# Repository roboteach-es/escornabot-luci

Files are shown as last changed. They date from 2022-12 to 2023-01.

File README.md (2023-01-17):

# Escornabot Luci

En base á nosa propia experiencia docente co [**Escornabot Brivoi**](https://www.escornabot.org/wiki/index.php?title=Archivo:Brivoi-001.jpg), xurdiu a necesidade de crear unha nova *subespecie* (ou versión). Baseada no Brivoi, incorporámoslle un sistema de **alimentación recargable** que axuda en varias frontes:

1. Supresión das pilas (aforro económico e ecolóxico)
2. Maior tempo de uso (maior cantidade de enerxía)
3. Facilidade de uso (basta con recargar, sen montar/desmontar para cambiar pilas)
4. Ideal para facer reciclaxe (cargadores de móbil, baterías de portátiles etc.)

Somos conscientes tamén das contraindicacións do emprego de baterías, e tivéronse en conta á hora de deseñar esta subespecie (por exemplo, **a seguridade**). Tamén coidamos todo o posible **o equilibrio** entre a dificultade de fabricación, o coste dos materiais e a usabilidade/practicalidade, xa que un dos obxectivos fundamentais é **a ACCESIBILIDADE** (en sentido amplo!).

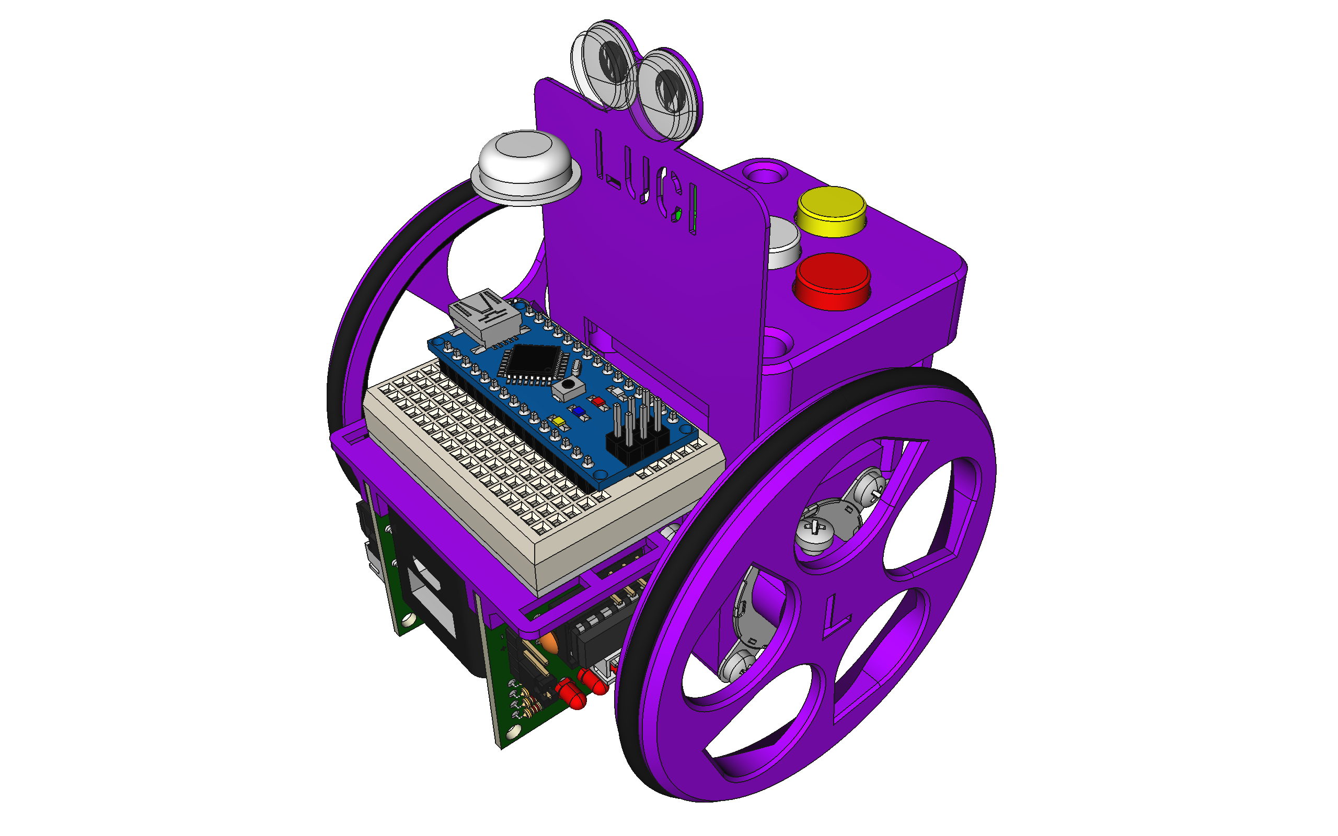
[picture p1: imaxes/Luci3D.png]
Luci 3D

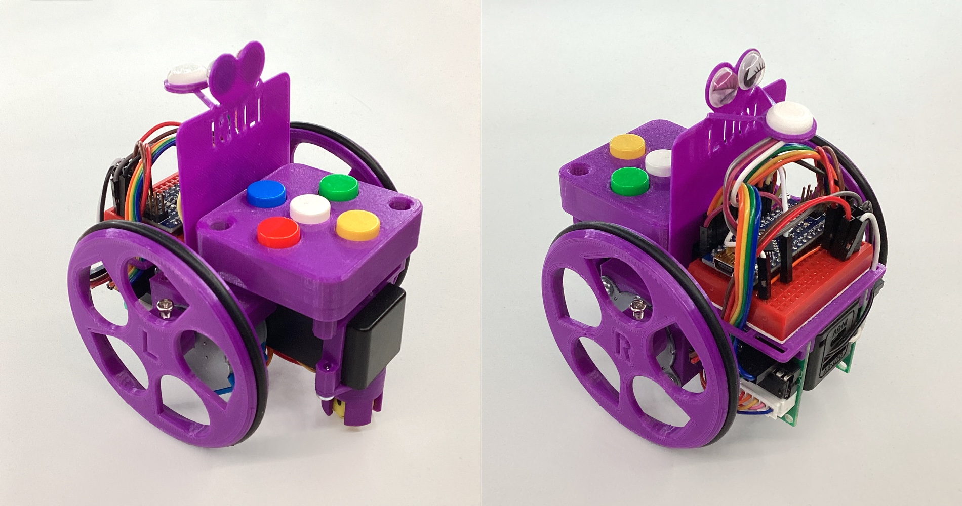
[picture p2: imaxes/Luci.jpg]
Luci prototipo


Continuando coa tradición do sistema de nomeclatura do proxecto Escornabot, decidimos bautizalo empregando unha das subespecies, escollendo a [subespecie **Luci**](https://species.wikimedia.org/wiki/Lucanus_luci) por tratarse dun nome **feminino** e relativo á **luz**. E a cor identificativa: **violeta** (claramente! 🙆🏽‍♀️😊)

## NOVIDADES

**Luci** trae unhas cantas novidades:

* **Batería recargable**, gracias a un *PowerBank-DIY*
* **LED RGB**, gracias a un *NeoPixel*
* **Chasis 3D**, adaptado ao novo sistema de alimentación
* **Firmware**, para dar soporte ás novas funcións
* **Biblioteca programable**, na que se basea o *Firmware*

Físicamente, **Luci** é moi similar ao **Brivoi** do que parte, con apenas 5 mm de ancho adicionais, conservando o **factor de forma** que todas coñecemos (e tanto nos gusta), polo que podes usalo exactamente **igual que o anterior**. Leva a mesma cantidade de tornillos e segue sendo igual de fácil de montar. O **coste de fabricación** tamén é moi similar, incluso mais económico se consegues facer **reciclaxe de baterías**. A maior vantaxe económica (e ecolóxica) é, sen embargo, o **aforro a longo prazo**, xa que podes recargalo e non terás que mercar (nin tirar) mais pilas.

**Luci** está en continuo desenvolvemento, e ainda é un *traballo en marcha*: se descubres calqueira problema, ou queres facer algunha aportación, por favor **contacta con nos**, estaremos encantadas de saber de ti.

## QUERO UN, como fago?

Se queres un **Escornabot Luci** podes acudir á [**guía de fabricación**](FABRICACIÓN.md) para facerte tantos como queiras: nela explicamos todo o necesario, dende a merca de compoñentes, pasando pola impresión 3D ate a reciclaxe de baterías.

## INFORMACIÓN

O proxecto **Luci** está conformado por diversos apartados que se recollen a continuación:

### HARDWARE

Na carpeta [`3D`](3D) atoparás todos os **modelos 3D** editables das pezas, creadas usando [FreeCAD](https://freecad.org). Tamén están dispoñibles os **ficheiros STL**, listos para ser impresos en 3D.

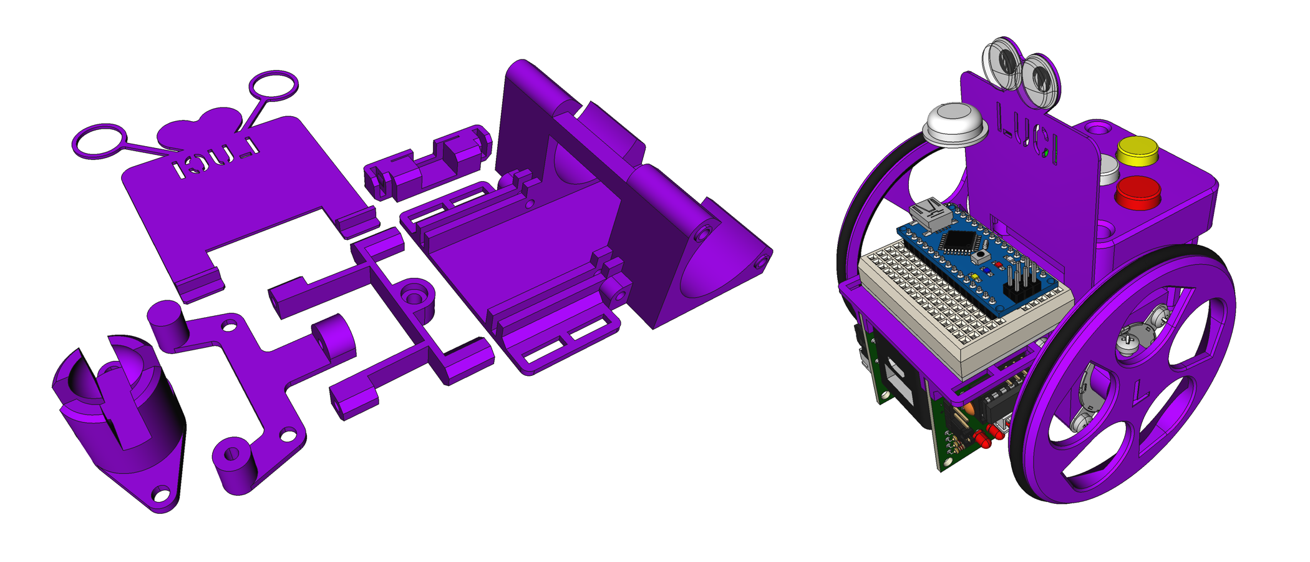
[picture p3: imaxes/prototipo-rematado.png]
Pezas3D


O compoñente central de Luci é o [PowerBank-DIY](POWERBANK.md), que está documentado no seu propio apartado.

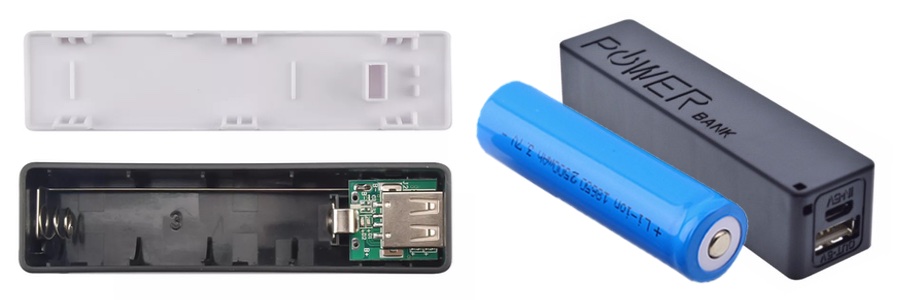
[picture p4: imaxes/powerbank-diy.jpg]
PowerBank-DIY


Na carpeta [`Electrónica`](Electrónica) atoparás o esquema de conexionado, creado con [Fritzing](https://fritzing.org).

Connections

### SOFTWARE

Na carpeta [`Programación`](Programación) atoparás todo o relativo ao apartado de programación, ainda que a [**biblioteca programable e o Firmware**](https://github.com/roboteach-es/escornabot-lib) teñen o seu propio repositorio específico.

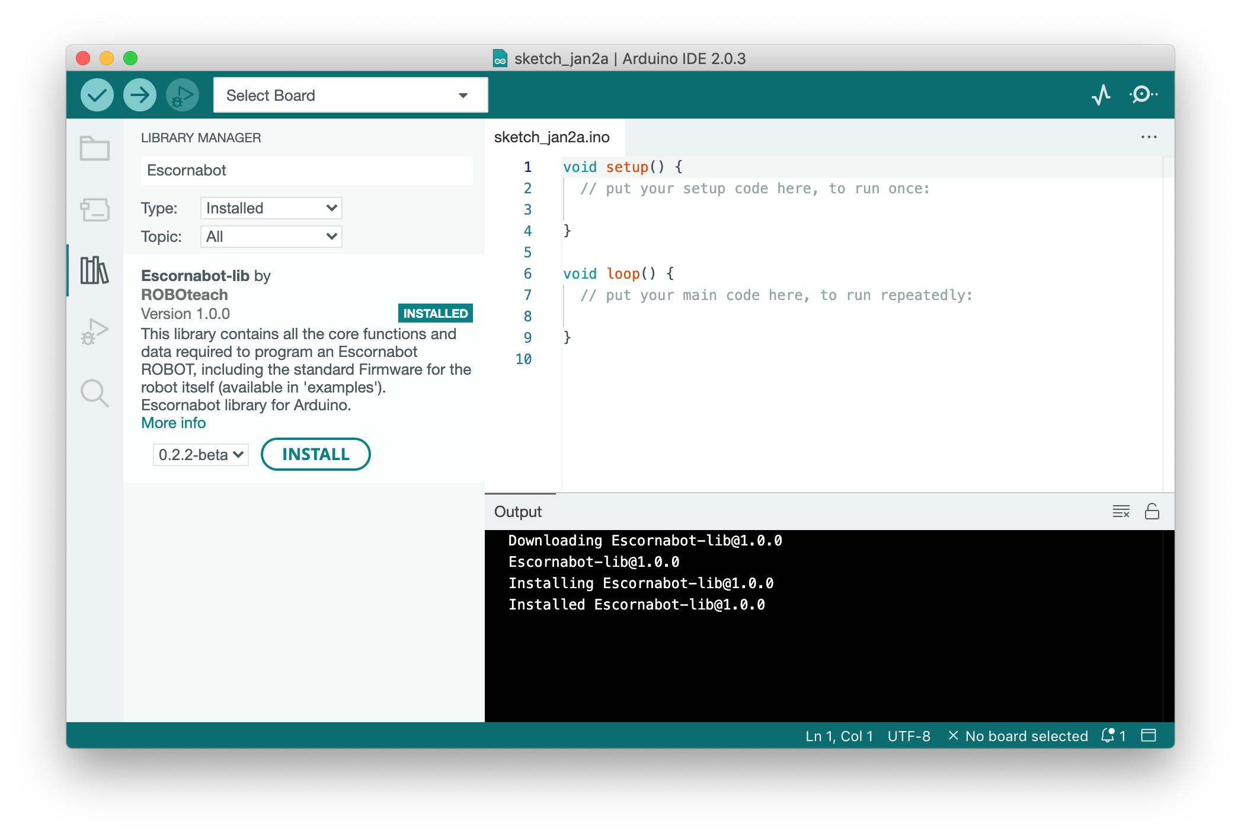
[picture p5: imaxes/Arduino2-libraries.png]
Biblioteca Arduino (https://github.com/roboteach-es/escornabot-lib)


### BITÁCORA

Se queres saber detalles do desenvolvento, levamos unha especie de bitácora que [podes ler](DESENVOLVEMENTO.md).

## LICENZA

Este traballo está suxeito á licenza [GNU General Public v3.0 License](LICENSE-GPLV30). Todos os ficheiros multimedia e de datos que non sexan código fonte están suxeitos á licenza [Creative Commons Attribution 4.0 BY-SA license](LICENSE-CCBYSA40).

Máis información acerca destas licenzas en [licenzas Opensource](https://opensource.org/licenses/) e [licenzas Creative Commons](https://creativecommons.org/licenses/).

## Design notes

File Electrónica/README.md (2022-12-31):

# Escornabot Luci - Electrónica

Este é o esquema de conexións de **Luci**:

Conexionado Luci

Está feito con [Fritzing](https://fritzing.org) e tes o ficheiro editable [dispoñible para descarga](Luci_conexi%C3%B3ns.fzz).

Este é o resumo de conexións entre os pins de cada **dispositivo** (á esquerda) e os pins do **Arduino Nano** (á dereita):

* **Motor Esquerdo**:
	* `IN1 ⟶ D4`
	* `IN2 ⟶ D5`
	* `IN3 ⟶ D6`
	* `IN4 ⟶ D7`
	* `GND ⟶ GND`
	* `VCC ⟶ 5V`
* **Motor Dereito**:
	* `IN1 ⟶ D8`
	* `IN2 ⟶ D9`
	* `IN3 ⟶ D10`
	* `IN4 ⟶ D11`
	* `GND ⟶ GND`
	* `VCC ⟶ 5V`
* **Teclado**:
	* `SIG ⟶ A0`
	* `GND ⟶ GND`
* **Buzzer**:
	* `PIN1 ⟶ GND`
	* `PIN2 ⟶ D2`
* **Neopixel**:
	* `IN  ⟶ D12`
	* `GND ⟶ GND`
	* `VCC ⟶ 5V`
* **PowerBANK-DIY**:
	* `5V  ⟶ 5V`
	* `GND ⟶ GND`

Para poder ter suficientes puntos de conexión para 5V e GND, hai un par de cables (os que están horizontais) que levan estes pins a cada unha das columnas laterais da *mini-breadboard*.

## Arduino Nano

**Luci** emprega un microncontrolador Arduino Nano como *cerebro* para o seu funcionamento. Aquí tes unha referencia dos pins do mesmo:

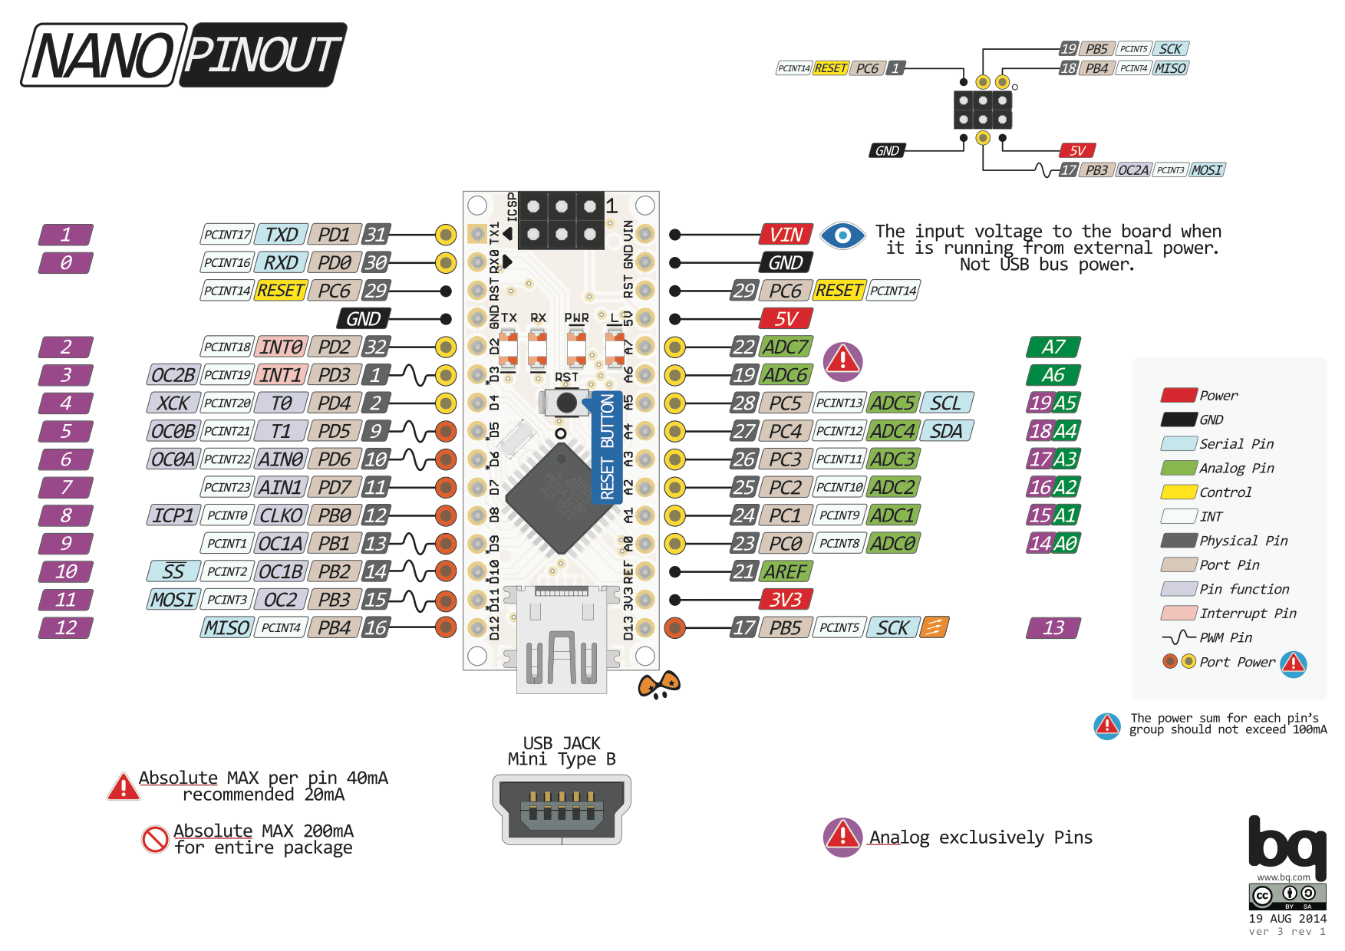
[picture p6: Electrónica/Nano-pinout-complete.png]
Arduino Nano pins


## LICENZA

Este traballo está suxeito á licenza [GNU General Public v3.0 License](../LICENSE-GPLV30). Todos os ficheiros multimedia e de datos que non sexan código fonte están suxeitos á licenza [Creative Commons Attribution 4.0 BY-SA license](../LICENSE-CCBYSA40).

Máis información acerca destas licenzas en [licenzas Opensource](https://opensource.org/licenses/) e [licenzas Creative Commons](https://creativecommons.org/licenses/).

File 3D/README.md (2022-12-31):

# Escornabot Luci - 3D

Este é o modelo 3D de **Luci**:

Luci

Estas son as pezas novas para esta subespecie:

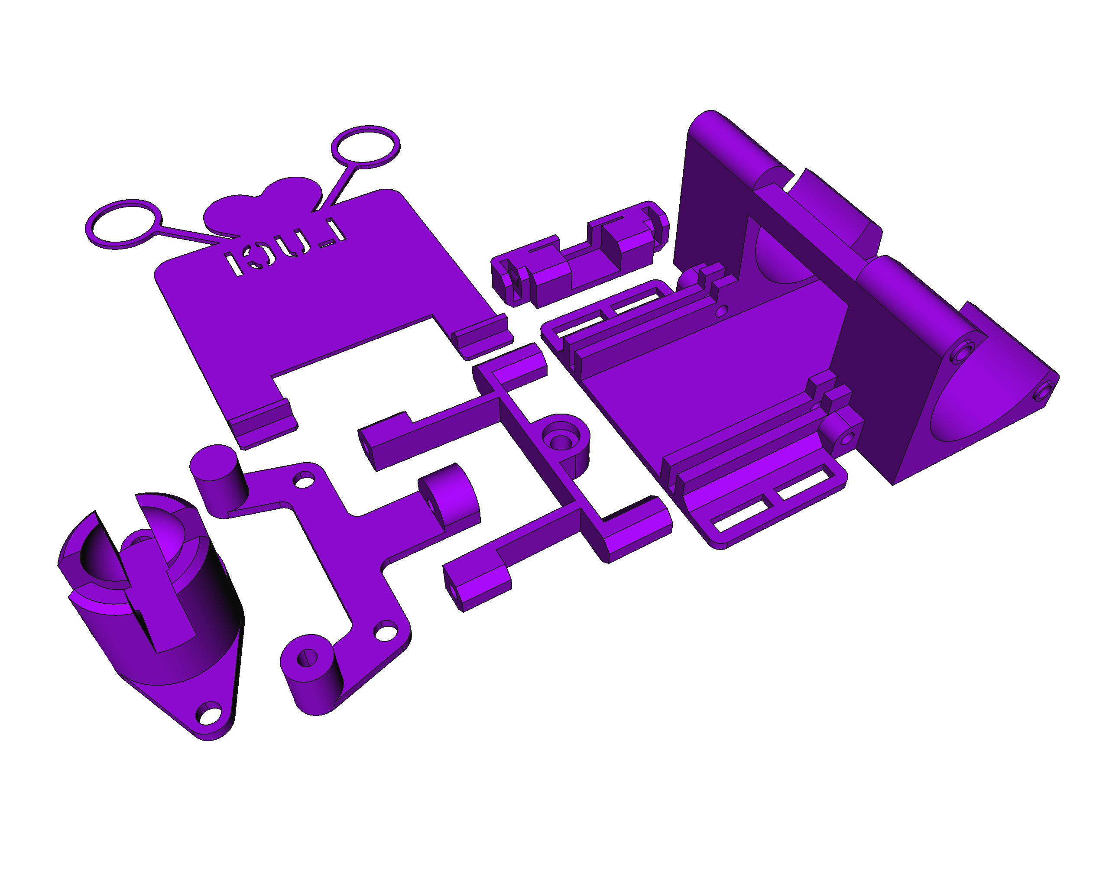
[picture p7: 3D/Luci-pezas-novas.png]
Novas pezas


de esquerda a dereita: **porta-bola**, **carauta NeoPixel**, **soporte teclado**, **soporte porta-bola**, **soporte interruptor** e **chasis**.

## Modelos 3D editables

Todos os modelos 3D foron creados coa ferramenta open-source [FreeCAD](https://www.frecad.org), e están dispoñibles para a súa edición:

* [`Escornabot-Luci.FCStd`](Escornabot-Luci.FCStd), modelo principal (o da imaxe) que contén tódalas novas pezas
* [`keypad-cover.FCStd`](keypad-cover.FCStd), a coberta do teclado
* [`wheel-left.FCStd`](wheel-left.FCStd) e [`wheel-right.FCStd`](wheel-right.FCStd), as rodas
* [`wheel-base.FCStd`](wheel-base.FCStd), a roda base, por se queres personalizala
* [`Escornaface-NeoPixel.FCStd`](Escornaface-NeoPixel.FCStd), carauta separada, por se queres personalizala

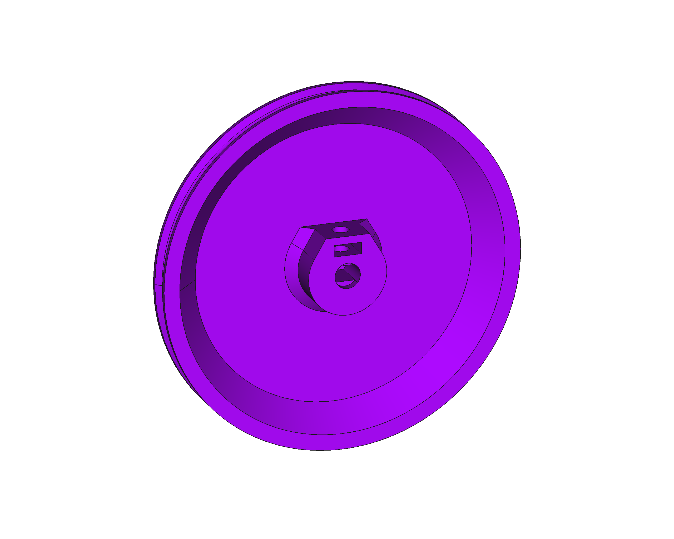
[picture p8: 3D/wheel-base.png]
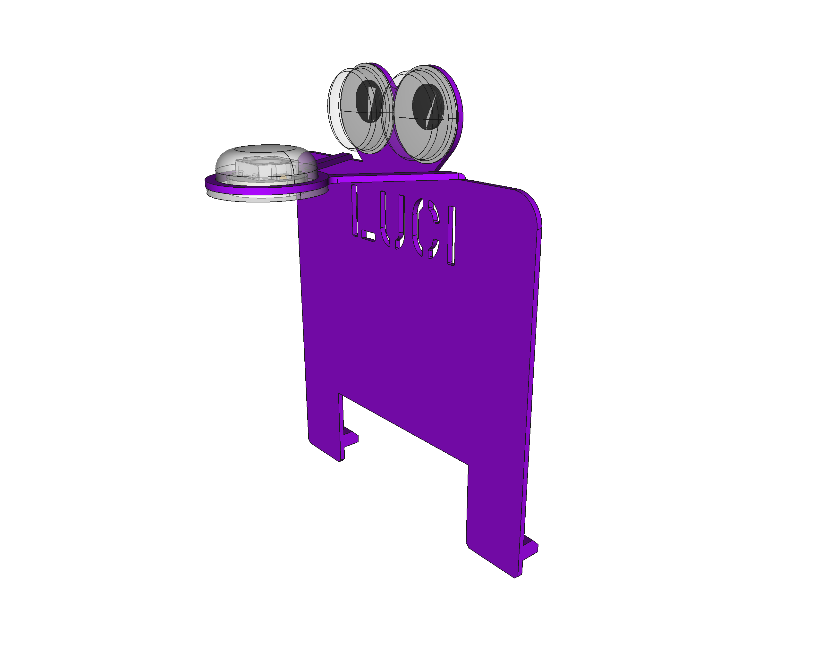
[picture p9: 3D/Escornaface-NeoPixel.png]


## Listado STL

Na carpeta [`stl`](stl) poderás atopar todos os ficheiros das 10 pezas, listas para ser impresas con calqueira impresora 3D.

Pezas novas:

* [`Porta-bola`](stl/luci-ballcaster.stl)
* [`Carauta NeoPixel`](stl/luci-escornaface-NP.stl)
* [`Soporte teclado`](stl/luci-keypad-chasis-support.stl)
* [`Soporte porta-bola`](stl/luci-keypad-ballcaster-support.stl)
* [`Soporte interruptor`](stl/luci-switch-holder.stl)
* [`Chasis`](stl/luci-chasis.stl)
* [`Cápsula NeoPixel`](stl/luci-neopixel.stl) (non aparece na imaxe anterior)

Pezas reutilizadas:

* [`Roda esquerda`](stl/wheel-left.stl)
* [`Roda dereita`](stl/wheel-right.stl)
* [`Cubre teclado`](stl/keypad-cover.stl)

## LICENZA

Este traballo está suxeito á licenza [GNU General Public v3.0 License](../LICENSE-GPLV30). Todos os ficheiros multimedia e de datos que non sexan código fonte están suxeitos á licenza [Creative Commons Attribution 4.0 BY-SA license](../LICENSE-CCBYSA40).

Máis información acerca destas licenzas en [licenzas Opensource](https://opensource.org/licenses/) e [licenzas Creative Commons](https://creativecommons.org/licenses/).

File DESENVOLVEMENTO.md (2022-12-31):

# DESENVOLVENTO de Luci

Algunhas notas sobre o proceso de desenvolvemento de Luci. Non é algo riguroso ou
sistemático, soamente unha especie de *bitácora*.

## Arrinque
O desenvolvemento de **Luci** comezou a finais do 2021: fartas do problema das
pilas decidimos intentar -en serio(™)- facer unha versión baseada nun
[*powerbank-DIY*](POWERBANK.md), reutilizando celas 18650 Li-ion recicladas de
baterías de portátiles vellos ou estropeados.

powerbank-diy

O obxectivo era facelo **accesible**, simple e o mais seguro posible:

* Compoñentes económicos e fáciles de atopar
* Montaxe simple, apto para calqueira nivel
* Seguro, empregando kits prefabricados con mecanismos de protección
* Principio das múltiples R (Reducir, Reutilizar, Reciclar, Recuperar, Reparar ...)
* Principio de deseño [KISS](https://en.wikipedia.org/wiki/KISS_principle)

Empezamos collendo os compoñentes físicos e posicionandoos, probando distintas
configuracións para tratar de ver que funcionaba e que sensacións tiñamos, discutindo
sobre que podería funcionar ou que problemas poderiamos ter.

## 1 xaneiro 2022
A última acción do 2021 e primeira do 2022 foi publicar o repositorio git do
proxecto en [github](https://github.com/roboteach-es/escornabot-luci): tratábase
dunha proba de concepto onde, nun modelo 3D en [FreeCAD](https://freecad.org),
posicionamos todos os compoñentes de Luci (motores+drivers, mini-breadboard+arduino,
teclado, rodas, bola-tola e powerbank) tal e como decidiramos na discusión previa.

Foi o nacemento **oficial e formal** público do proxecto.

## 8-9 decembro 2022
**Despois de case un ano** sen ningunha actividade, retomouse o deseño 3D en FreeCAD
para tratar de crear un chasis funcional. Partindo do traballo previo, fixéronse
ata tres versións distintas con múltiples iteracións para axustar pequenas cousas,
ata chegar ao primeiro esqueleto que permitía montar todos os compoñentes.

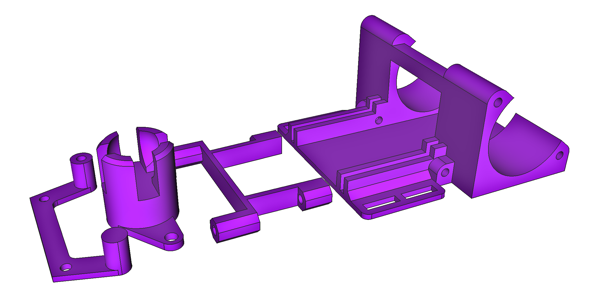
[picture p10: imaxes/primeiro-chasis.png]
primeiro chasis


O mais salientable é que a peza do chasis, a pesar desa ponte de 25mm, pódese imprimir 
perfectamente sen soportes (nunha impresora básica calqueira como pode ser a *Ender-3*).

## 10 decembro 2022
Probando o primeiro prototipo apareceron algúns problemas, as veces menores e
outros non tanto:

* **Equilibrio**: Luci balacéase con facilidade, xa que a cela 18650 non pesa
  tanto como as pilas e o centro de gravidade esta moi próximo aos eixos de
  rotación no punto central. Cun pequeno refinamento mellorou, pero seguirá
  sendo a mais equilibrista (o que pode acabar convertíndose no seu selo de
  identidade 😅💃🏽)
* **Cables**: *arboran* con facilidade e os conectores dupont deron moita guerra
   co espacio que ocupan. Cunhas pequenas guías para os cables e algúns axustes de
  posición, acabaron encaixando.
* **Autoapagado**: a maioría dos *powerbank* teñen unha función de autoapagado
  e se desconectan se non detectan suficiente consumo de enerxía. O consumo de
  Luci en reposo non é suficiente para evitalo, e este problema... non é trivial.

### Autoapagado
Cando Luci está en movemento, o consumo (dos motores) é suficiente alto e non hai
problema, pero o tempo de reposo máximo é pequeno (uns poucos segundos) e, ademáis,
o comportamento varía dun powerbank a outro:

* **HT4928S**: estando Luci en reposo e, aproximadamente aos 12 seg., salta o
  autoapagado. Unha vez apagado, actívase o modo de detección de "nova conexión" e,
  como hai algo conectado, volve a acenderse. É dicir, temos un círculo vicioso de
  reinicios cada 12 seg.: non consume o suficiente para manterse acendido pero
  si consume o suficiente para reacenderse. 🤷🏽‍♂️
* **TP4333**: o consumo mínimo é maior, pero cando se apaga, realmente queda
  apagado (non se reinicia).

Ambos comportamentos teñen os seus PROs e CONTRAs, e barállanse varias opcións
para "resolvelo":

* engadir unha carga paralela permanente (LEDs)? (maior consumo, mais complexidade...)
* incluir no *firmware* un sistema *anti-reposo* como, por exemplo, acender bobinas
  periódicamente en caso de inactividade (probablemente a opción menos mala...)
* en último caso... facer un powerbank dende cero? (non cumpre o principio KISS)

En calqueira caso, un firmware novo é unha tarefa longamente requerida (e
postergada)...

## 11-12 decembro 2022
Prototipo inicial rematado, con algunhas modificacións extra e un par de novas
pezas: soporte do interruptor e a carauta.

powerbank-diy

Agora hai que deixalo *"respirar"* e probar a usalo **no campo** para descubrir
que cousas hai que corrixir ou mellorar. Algún *early-adopter* léndonos?

**PROBLEMAS:** o conector USB queda escondido trala roda (hai que quitala para poder
conectar o cable).<br />
**PORFACER:** programar un novo firmware con anti-reposo.

## 16-25 decembro 2022
**Luci** non ía ser moi útil sen software, e os problemas, complexidade e
sobre-enxeñería do [firmware *oficial*](https://github.com/escornabot/arduino),
non convidaban a seguir *meténdolle mais horas(™)*, así que creamos unha
[*suite* **completamente nova**](https://github.com/roboteach-es/escornabot-lib),
partindo dende cero e aproveitando a experiencia recollida, primeiro do firmware
anterior (que ten moitas cousas boas) e, sobre todo, da nosa propia labor
\[docente\] de campo, tras empregar o Escornabot en moitos e moi variados
escenarios formativos e didácticos.

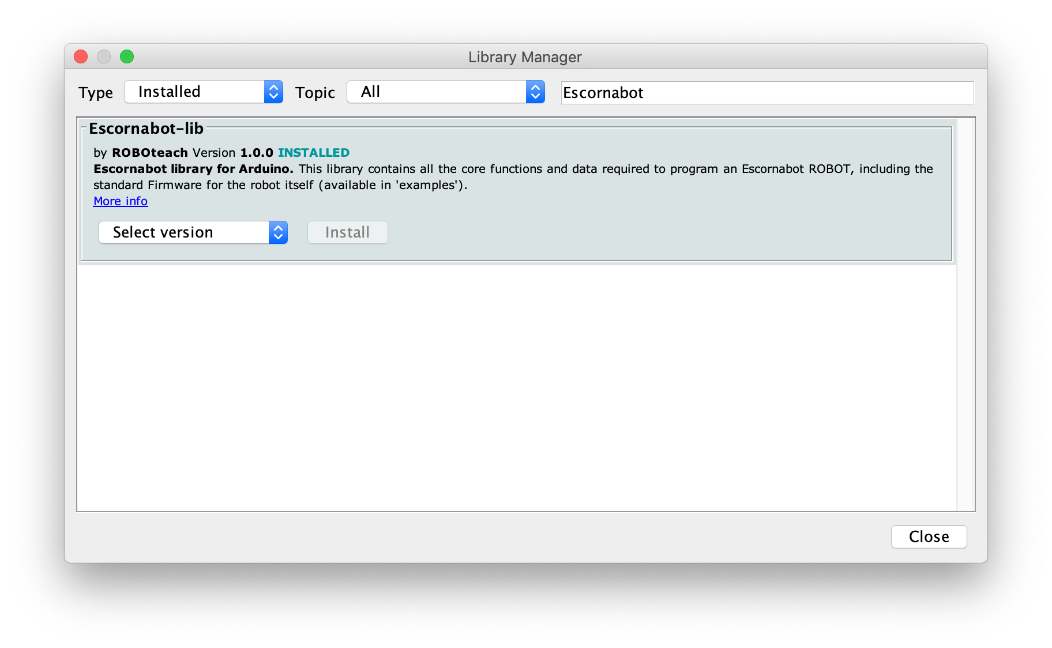
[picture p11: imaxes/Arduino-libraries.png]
Escornabot-lib


Esta nova *suite* está publicada a través da propia **plataforma de Arduino**,
de maneira que aparece como unha bibliteca instalable directa e automaticamente
a través do [seu IDE](https://www.arduino.cc/en/software). Componse de:

* unha **biblioteca base** que recolle todas as funcionalidades fundamentais
* un conxunto de **exemplos** onde se ilustra o seu emprego
* un novo **firmware** que está escrito a partires dela

Deste xeito, ademáis de simplificarse moito, abstráese o núcleo, o que resulta
moi convinte para outras áreas como a integración con ferramentas de terceiros
(por exemplo, a contorna de programación visual *mBlock-3* &rarr; `TODO`).

O novo sistema está deseñado **específicamente para Luci** e, para poder
alcanzar o que nos propusimos inicialmente, hai certos aspectos que son únicos
e \[inicialmente\] incompatibles co anteriormente existente:

* novo [**esquema de conexionado**](Electrónica) optimizado para Luci (alimentación 5V)
* sistema de control de motores optimizado ([empregando
  *PORTx*](https://github.com/mgesteiro/steppers#portx-vs-digitalwrite))
* resolución do [**problema do autoapagado**](#autoapagado) dos *powerBank*
* control de inactividade
* autoconfiguración do teclado
* incorporación dun NeoPixel (LED RGB)
* resolución de problemas de interfaz e UX (botón azul)
* e soporte correcto para RTTTL

Esta suite está xa dispoñible no seu propio 
[repositorio **Escornabot-lib**](https://github.com/roboteach-es/escornabot-lib).

## 30-31 decembro 2022
Último millón de axustes e READMEs y mil pequenas cousas mais para a publicación
final de **Luci**: xusto **un ano despois**.

Queda moito por facer, pero é unha boa base de partida, con moitos **hitos
importantes** alcanzados:

* Prototipo hardware rematado e validado (pódese fabricar!)
* Suite de software completa, con todas as funcionalidades orixinais (pódese programar!)
* Documentación base rematada (está documentado!)

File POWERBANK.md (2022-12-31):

# PowerBank-DIY

Unha pequena *intro* aos **PowerBank-DIY** (_**D**o **I**t **Y**ourself_ = Faino Ti Mesma): son kits para fabricarte as túas propias *baterías-recargables* empregando -tipicamente- celas estándar 18650 Li-ion. O kit trae unha caixa contenedora (normalmente de ABS) cunha tapa autopechante. Ten espazo para unha cela 18650 (**NON INCLUÍDA**) e leva incorporada unha pequena circuitería electrónica (con **dous portos USB** distintos) que se encarga de toda a xestión.

powerbank-diy

A **carga** do PowerBank-DIY efectúase a través do porto **micro-USB**, empregando -por exemplo- un cargador de móbil (dos antigos). A nerxía extráese (**descarga**) a través do porto USB estándar, que proporciona **~5.1V** e **~0.8A**, ideais para **Luci**.

## ELECTRÓNICA

Atopamos que prácticamente tódolos *powerbanks* deste formato están baseados
nos chips electrónicos de dous fabricantes, con características similares e
varios mecanismos de protección incorporados moi interesantes (cortacircuito,
sobre-carga, sobre-descarga etc.):

* [HOTCHIP HT4928S](datasheet/HT4928S-HOTCHIP.pdf)
* [TPOWER TP4333](datasheet/TP4333-TPOWER.pdf)

A caixa contenedora é idéntica (ou prácticamente) entre distintos proveedores (imaxinamos que todos se copian entre si), o cal é moi convinte para poder cumprir algún dos requisitos iniciais. Por certo, a pesar da apariencia, a caixa non é rectangular senón lixeiramente prismática (propio da fabricación por moldes de inxección).

Na carpeta `3D`, o modelo 3D de **Luci** contén un submodelo bastante preciso (dimensionalmente falando) deste PowerBank-DIY.

## MODIFICACIÓN

[Nesta páxina de ROBOteach](https://www.roboteach.es/modificacion-power-bank/) temos unha guía para modificar o PowerBank-DIY e **dotalo dun par de cables dupont**, o que nos permitirá conectalo á nosa **Luci** (ou calqueira outro proxecto).



Require dun soldador, un pouco de estaño e algo de habilidade, pero nada esaxerado.

## CONSIDERACIÓNS

Escollimos este sistema porque é económico (o propio kit pode rondar os 2 €), é simple, e funciona bastante ben, proporcionando unha nova e **mellorada experiencia de uso** co Escornabot.

Ademáis, é bastante seguro:

* O contenedor plástico coa tapa autopechante proporciona unha capa de aillamento/protección adicional fronte a unha posible avaría da cela Li-ion 18650.
* O circuitería electrónica trae incorporadas múltiples proteccións:
	* **Anti-curtacircuito**: non pasa nada ainda que conectes os termináis dupont entre sí, xa que a electrónica desconéctase automáticamente ao detectalo (aforro dun fusible!)
	* **Anti-conexión inversa**: non pasa nada se conectamos os cables coa polaridade invertida
	* **Sobre-descarga**: o sistema evita que a batería se descargue mais aló do punto crítico (~3.4V)
	* **Sobre-carga**: tamén evita que se poida sobrecargar, xa que detén o proceso ao alcanzar a voltaxe máxima (~4.2V)
* E tamén algunhas funcións adicionais:
	* **Información de estado**: a través de dous LEDs, para indicarnos que está ocorrendo
	* **Reactivación de cela**: é capaz de recuperar unha cela 18650 totalmente descargada empregando o método *trickle-charge*
	* **Desconexión automática**: cando non hai consumo\*\*, para aforrar enerxía

\*\* Isto acabou converténdose nun [problema con **Luci**](DESENVOLVEMENTO.md#autoapagado), que xa foi resolto.

## LICENZA

Este traballo está suxeito á licenza [GNU General Public v3.0 License](LICENSE-GPLV30). Todos os ficheiros multimedia e de datos que non sexan código fonte están suxeitos á licenza [Creative Commons Attribution 4.0 BY-SA license](LICENSE-CCBYSA40).

Máis información acerca destas licenzas en [licenzas Opensource](https://opensource.org/licenses/) e [licenzas Creative Commons](https://creativecommons.org/licenses/).

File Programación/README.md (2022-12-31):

# Escornabot Luci - Programación

Nesta carpeta atoparás código, exemplos, tests e todo aquilo que teña que ver con programación para **Luci**, exceptuando a [**biblioteca programable** e o **Firmware**](https://github.com/roboteach-es/escornabot-lib) que teñen o seu propio repositorio específico.

* `old-firmware` é unha adaptación do firmware *"oficial"* do Escornabot ao conexionado de Luci.
* `test-steppers`, as primeiras probas usando acceso de baixo nivel **PORTx**
* `test-neopixel`, probas co NeoPixel
* `test-autoconfig`, probas para validar a autoconfiguración do teclado
* `mBlock-example`, an example code generated with mBlock-3 and ROBOteach Escornabot's extension: just for reference

## LICENZA

Este traballo está suxeito á licenza [GNU General Public v3.0 License](../LICENSE-GPLV30). Todos os ficheiros multimedia e de datos que non sexan código fonte están suxeitos á licenza [Creative Commons Attribution 4.0 BY-SA license](../LICENSE-CCBYSA40).

Máis información acerca destas licenzas en [licenzas Opensource](https://opensource.org/licenses/) e [licenzas Creative Commons](https://creativecommons.org/licenses/).

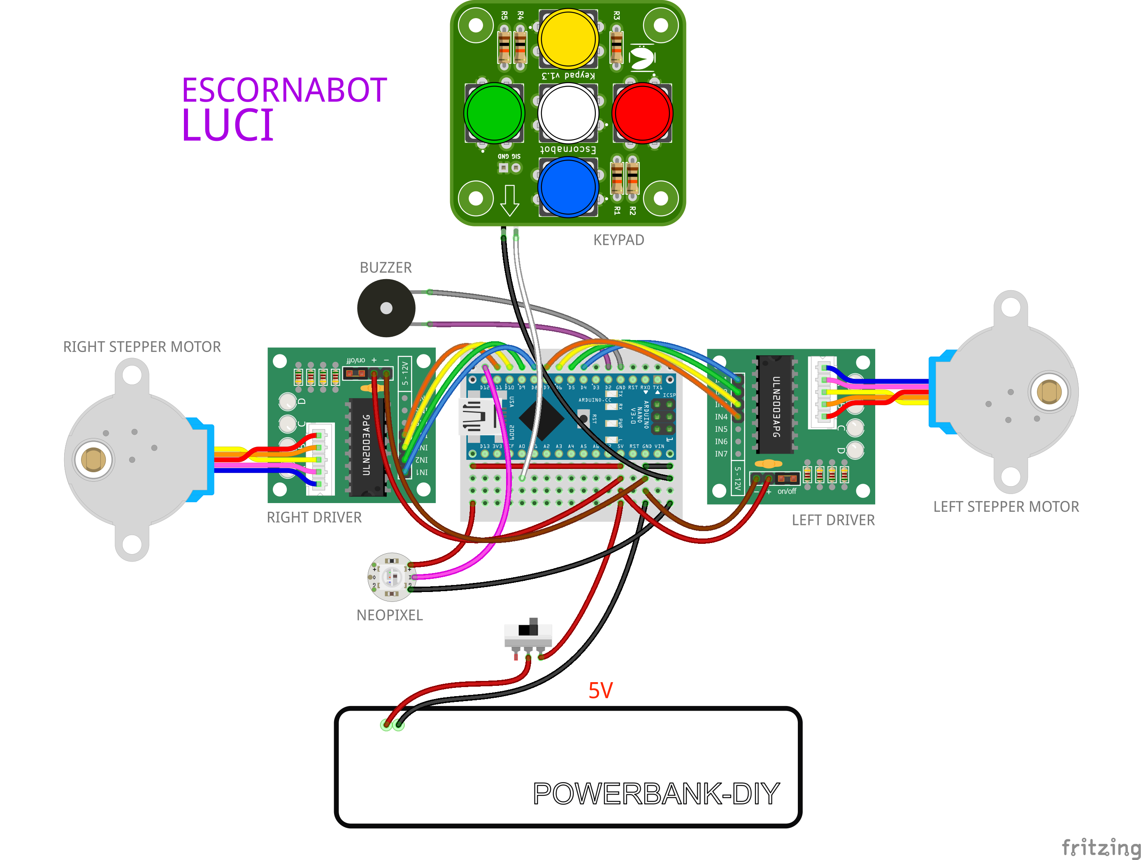
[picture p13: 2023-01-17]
Electrónica/Luci_conexións.png

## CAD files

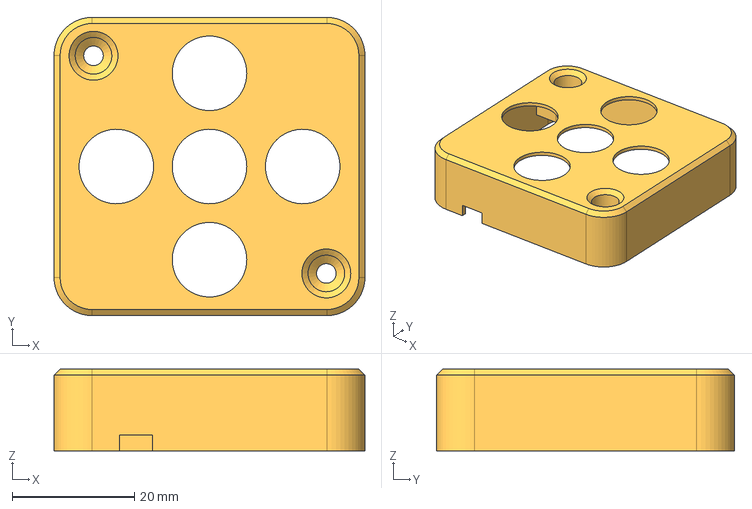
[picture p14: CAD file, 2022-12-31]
3D/keypad-cover.FCStd
50.9 x 48.8 x 13.4 mm

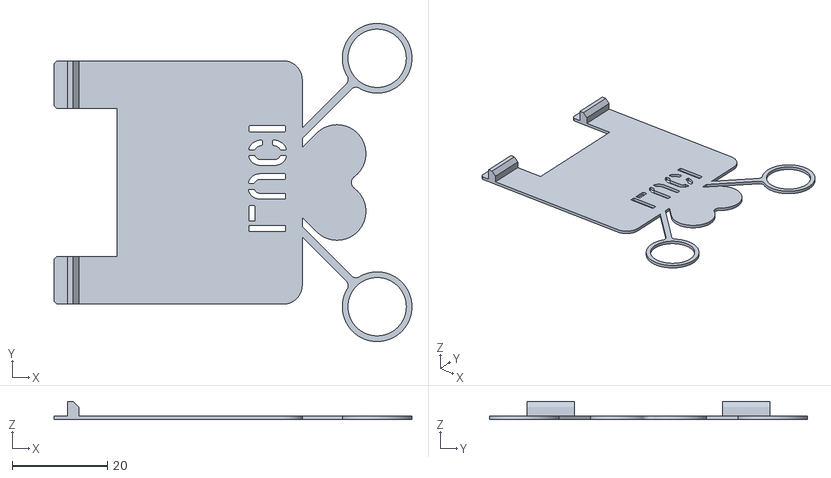
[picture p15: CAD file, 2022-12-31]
3D/stl/luci-escornaface-NP.stl
75.0 x 66.6 x 3.80

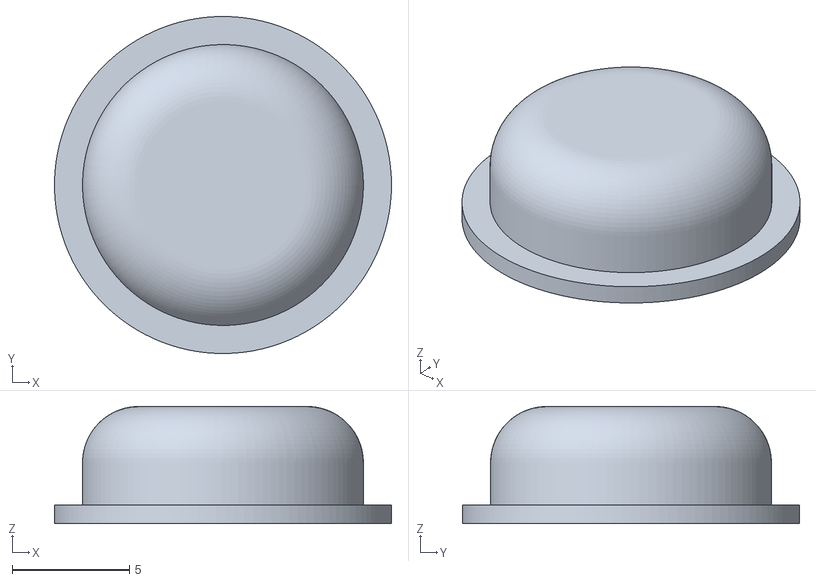
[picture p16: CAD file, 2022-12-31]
3D/stl/luci-neopixel.stl
14.4 x 14.4 x 5.00

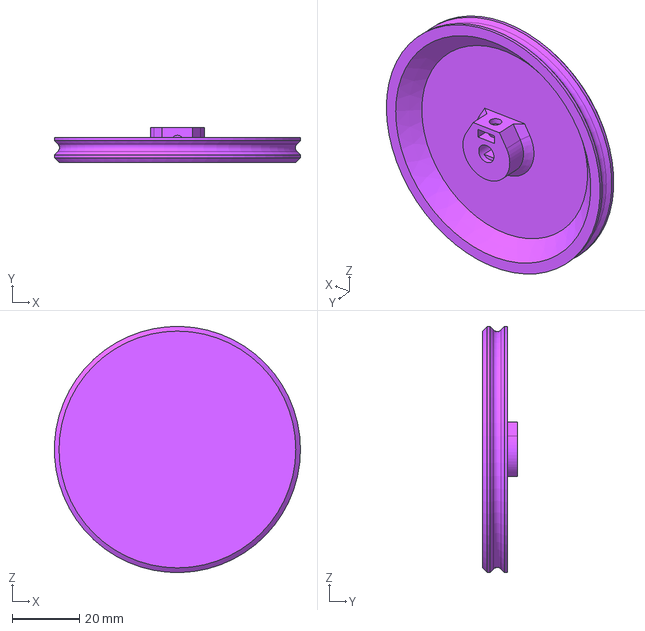
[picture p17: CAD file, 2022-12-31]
3D/wheel-base.FCStd
72.9 x 10.4 x 73.0 mm

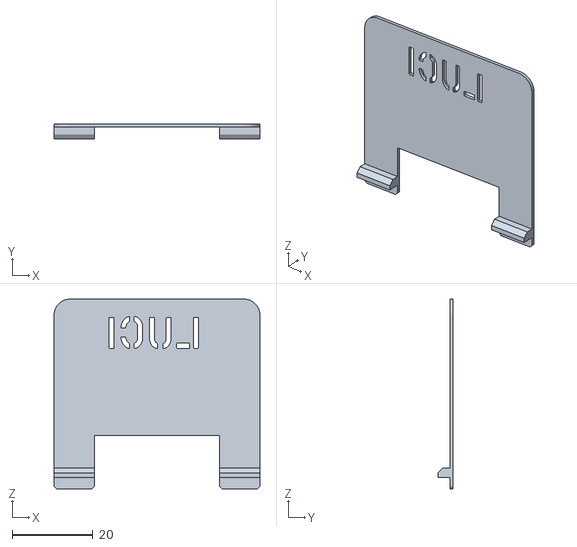
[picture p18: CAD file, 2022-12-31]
3D/stl/luci-escornaface.stl
51.0 x 3.80 x 47.0

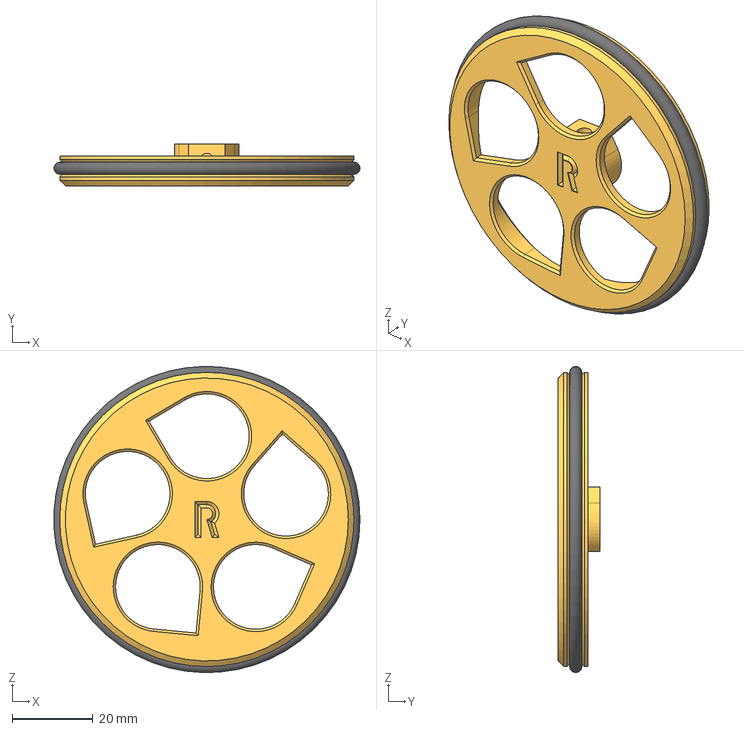
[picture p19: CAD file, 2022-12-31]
3D/wheel-right.FCStd
75.9 x 10.4 x 76.0 mm
Body-wheel-right
o-ring-R

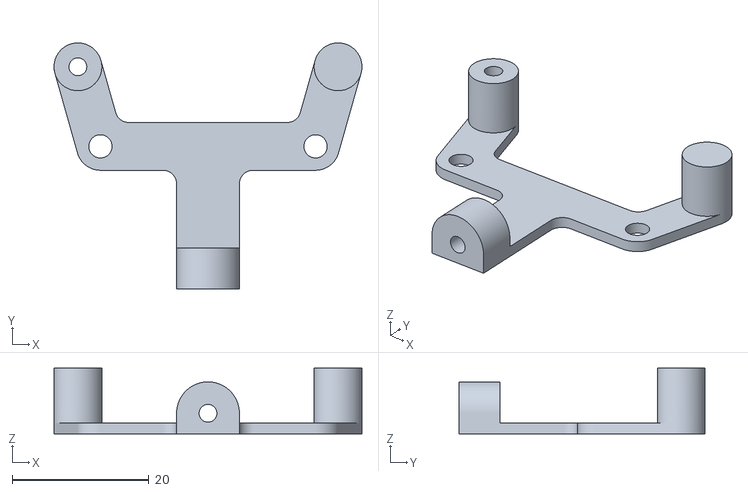
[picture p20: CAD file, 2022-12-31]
3D/stl/luci-keypad-chasis-support.stl
45.1 x 36.0 x 9.60

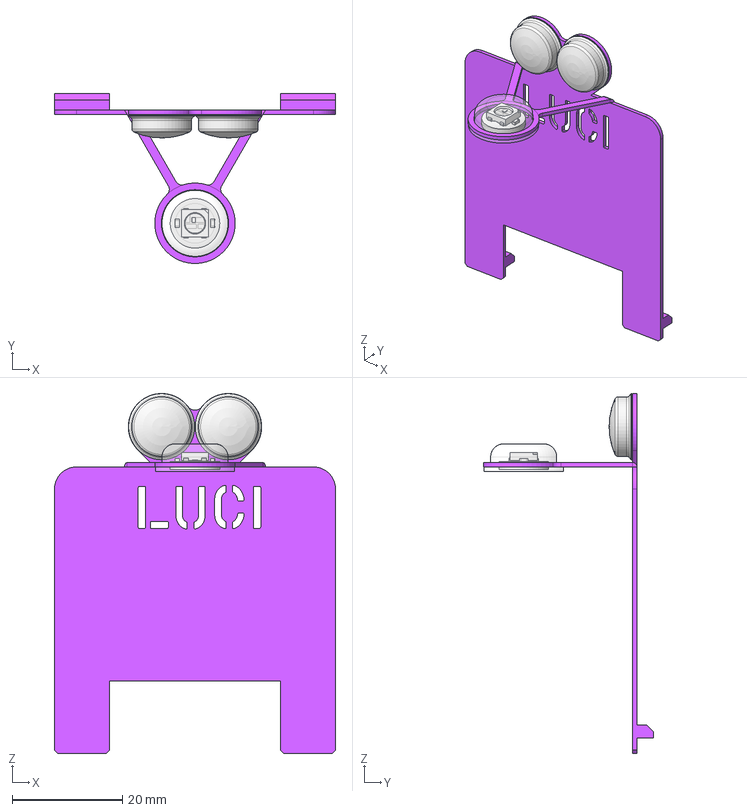
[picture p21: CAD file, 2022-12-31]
3D/Escornaface-NeoPixel.FCStd
51.0 x 30.8 x 65.3 mm
Body-RGB-cap
neopixel
right-eye
left-eye
Body-Simul

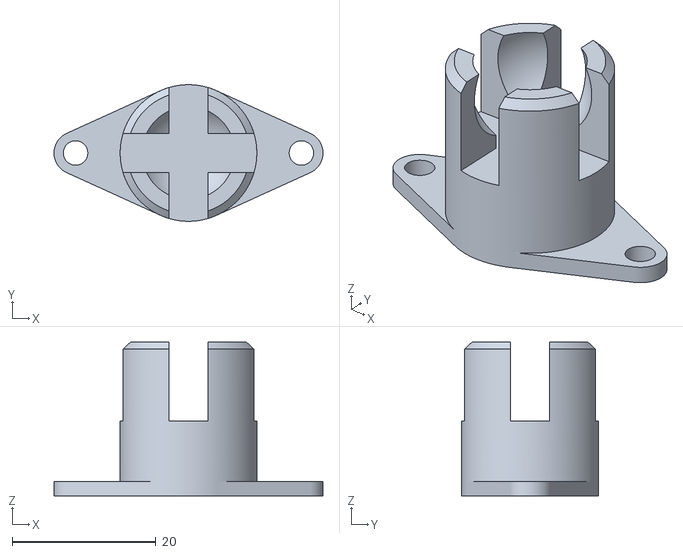
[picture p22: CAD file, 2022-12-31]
3D/stl/luci-ballcaster.stl
37.4 x 19.0 x 21.4

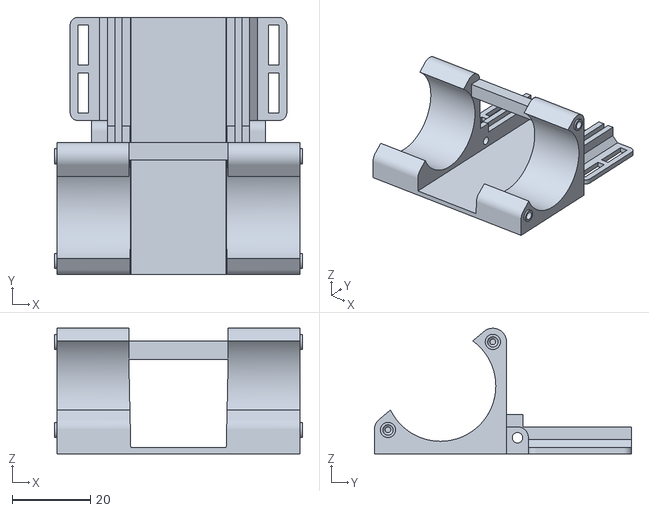
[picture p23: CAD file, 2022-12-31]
3D/stl/luci-chasis.stl
63.4 x 65.8 x 32.1

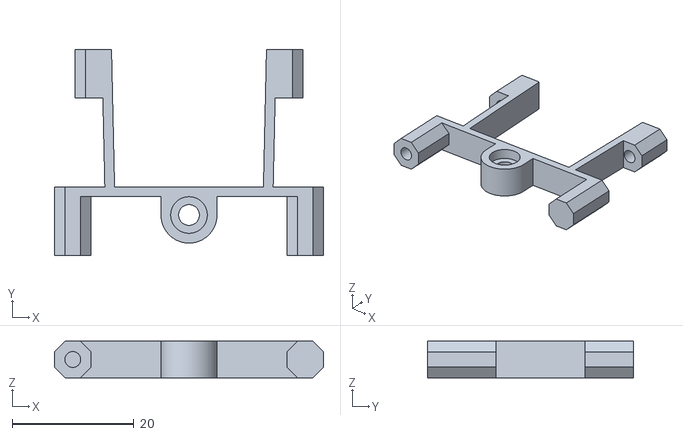
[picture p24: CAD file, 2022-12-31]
3D/stl/luci-keypad-ballcaster-support.stl
44.1 x 33.7 x 6.00

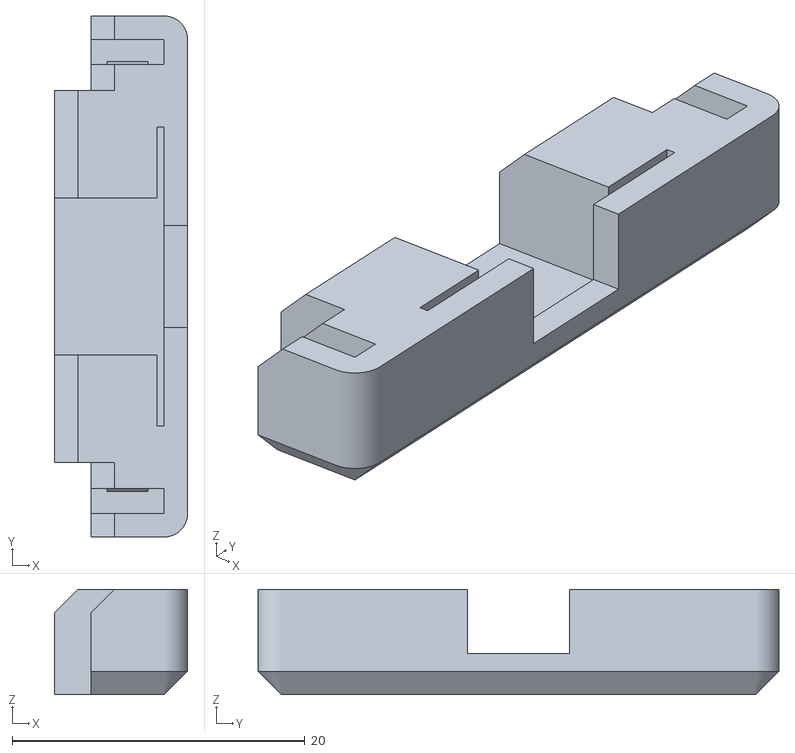
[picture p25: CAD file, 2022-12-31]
3D/stl/luci-switch-holder.stl
9.10 x 35.6 x 7.20

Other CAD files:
3D/wheel-left.FCStd
3D/stl/keypad-cover.stl
3D/stl/wheel-left.stl
3D/stl/wheel-right.stl

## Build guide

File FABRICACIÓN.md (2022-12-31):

# Escornabot Luci - Fabricación

Neste documento atoparás todo o necesario para poder crear a túa propia **Luci**.

## Compoñentes

## Reciclaxe de baterías

## Pezas 3D

## Ensamblado

## Conexionado

## Software

## LICENZA

Este traballo está suxeito á licenza [GNU General Public v3.0 License](LICENSE-GPLV30). Todos os ficheiros multimedia e de datos que non sexan código fonte están suxeitos á licenza [Creative Commons Attribution 4.0 BY-SA license](LICENSE-CCBYSA40).

Máis información acerca destas licenzas en [licenzas Opensource](https://opensource.org/licenses/) e [licenzas Creative Commons](https://creativecommons.org/licenses/).

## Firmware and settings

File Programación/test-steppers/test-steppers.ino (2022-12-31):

/*
 *   Testing Luci's stepper motors
 */

const static uint8_t state_sequence[] = {B0011, B0110, B1100, B1001}; // full drive
const static uint8_t delta_state_sequence = sizeof(state_sequence)-1;

// step tracking
int currentStateIndex = 0;
int stepDelay = 2500;


/*
 *   S E T U P   &   L O O P   F U N C T I O N S
 */

void setup() {
    initCoilsPins();
    // alive!
    tone(2, 4699, 100); // default beep
}

void loop() {
    // move forward indefinitely
    setCoils(state_sequence[delta_state_sequence-currentStateIndex], state_sequence[currentStateIndex]);
    currentStateIndex++;
    if (currentStateIndex>3) currentStateIndex=0;
    delayMicroseconds(stepDelay);
}


/*
 *   S U P P O R T   F U N C T I O N S
 */

/*
Luci configuration to simplify PORTx usage

#define STEPPERS_MOTOR_LEFT_IN1 4    // blue
#define STEPPERS_MOTOR_LEFT_IN2 5    // pink
#define STEPPERS_MOTOR_LEFT_IN3 6    // yellow
#define STEPPERS_MOTOR_LEFT_IN4 7    // orange
#define STEPPERS_MOTOR_RIGHT_IN1 8   // blue
#define STEPPERS_MOTOR_RIGHT_IN2 9   // pink
#define STEPPERS_MOTOR_RIGHT_IN3 10  // yellow
#define STEPPERS_MOTOR_RIGHT_IN4 11  // orange
*/
void initCoilsPins()
{
    // PORTB maps to Arduino digital pins 8 to 13. The two high bits (6 & 7) map to the crystal pins and are not usable.
    DDRB = DDRB | B00001111;  // pins x,x,x,x,11,10,9,8 as OUTPUT - Right motor
    // PORTD maps to Arduino digital pins 0 to 7. Pins 0 and 1 are TX and RX, manipulate with care.
    DDRD = DDRD | B11110000;  // pins 7,6,5,4,x,x,x,x as OUTPUT - Left motor
}

void setCoils(uint8_t stateR, uint8_t stateL)
{
    // PORTD maps to Arduino digital pins 0 to 7
    // RightMotor - pins 4,5,6,7   -> PORTD bits[7-4] = stateR bits[3-0]
    // (a & ~mask) | (b & mask)
    // a -> PIND  b->(stateR << 4)  mask->B11110000
    PORTD = (PORTD & B00001111) | ((stateL << 4) & B11110000);

    // PORTB maps to Arduino digital pins 8 to 13 The two high bits (6 & 7) map to the crystal pins and are not usable
    // LeftMotor  - pins 8,9,10,11 -> PORTB bits[3-0] = stateL bits[3-0]
    // (a & ~mask) | (b & mask)
    // a -> PINB  b->stateL  mask->B00001111
    PORTB = (PORTB & B11110000) | (stateR & B00001111);
}

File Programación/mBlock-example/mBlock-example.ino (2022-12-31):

#include <Arduino.h>
#include <Wire.h>
#include <SoftwareSerial.h>

#include "Escornabot.h"

double angle_rad = PI/180.0;
double angle_deg = 180.0/PI;
Escornabot escornabot;



void setup(){
    escornabot.turnLED(1);
    escornabot.beep(4699, uint16_t(0.1*1000));
    while(!(escornabot.isButtonPressed("GO")))
    {
        _loop();
    }
    
}

void loop(){
    
    escornabot.move(10);
    escornabot.beep(2637, uint16_t(0.1*1000));
    escornabot.turn(90);
    escornabot.beep(4434, uint16_t(0.1*1000));
    
    _loop();
}

void _delay(float seconds){
    long endTime = millis() + seconds * 1000;
    while(millis() < endTime)_loop();
}

void _loop(){
    
}

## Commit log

2022-01-01 First approach to components' assembly
2022-12-31 1 year update
    [Configuration.h, Escornaface-NeoPixel.FCStd, Luci_conexións.fzz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]
2023-01-17 Fritzing Powerbank-DIY
    [Luci_conexións.fzz]
